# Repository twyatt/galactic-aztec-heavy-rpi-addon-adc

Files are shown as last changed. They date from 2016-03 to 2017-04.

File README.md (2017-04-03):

# About
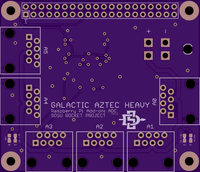
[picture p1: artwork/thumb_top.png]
OSHPark PCB Top Thumbnail

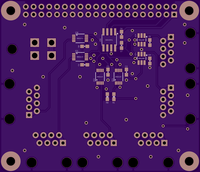
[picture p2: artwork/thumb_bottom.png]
OSHPark PCB Bottom Thumbnail


Custom Raspberry Pi Add-on ADC board (based on the [Galactic Aztec Raspberry Pi Add-on: Pressure Transducer Interface] board) used to read pressures on the [Galactic Aztec Heavy] rocket. The board has a molex connector for power input (Supply Voltage) and 6 ethernet ports for interfacing with custom [pressure transducer connector boards].

Custom EagleCAD parts on this board can be found in the [SDSU Rocket Eagle Libraries].

## Specifications
| Input | IC |
|:-----:|:---:|
| A0 | ADS1114 |
| A1 | ADS1114 |
| A2 | ADS1114 |
| A3 | ADS1114 |
| A4 | ADS1100 |
| A5 | ADS1100 |

### ADS1114
16-bit, 860 SPS ADC

| PGA | Resolution (V) | Maximum Input (V) |
|:---:|:---|:---:|
| 2/3 | 0.0001875 | 5.3 |
| 1 | 0.000125 | 4.096 |
| 2 | 0.0000625 | 2.048 |
| 4 | 0.00003125 | 1.024 |
| 8 | 0.000015625 | 0.512 |
| 16  | 0.0000078125 | 0.256 |

### ADS1100
| Bits | Resolution (V) | Sample Rate (SPS) |
|-----:|:---|:---:|
| 16 | 0.000152587891 | 8 |
| 15 | 0.000305175782 | 16 |
| 14 | 0.000610351563 | 32 |
| 12 | 0.00244140625  | 128 |

_Resolution values listed with PGA=1_

## Wiring
The ethernet ports adhere to the following [T-568B] wiring configuration:

| Pin | Color | Function |
|:---:|:---:|:---:|
| 1 | Orange/White | Signal |
| 2 | Orange | Signal |
| 3 | Green/White  | |
| 4 | Blue | Supply Voltage |
| 5 | Blue/White | Supply Voltage |
| 6 | Green | |
| 7 | Brown/White  | Ground |
| 8 | Brown | Ground |

# Bill of Materials
| Qty | Name  | Description | Notes | Part Number | Vendor |
|:---:|:-----:|---|---|---|---|
| 1 | H0 | Header Stacking 2x20 Tall 23mm | | [1979] | Adafruit |
| 1 | P0 | Molex Mini Fit Jr. 4-pos Right Angle | | [WM1352-ND] | DigiKey  |
| 6 | JP0-5 | Jack RJ45 CAT5/CAT5e | | [380-1046-ND] | DigiKey  |
| 1 | IC6 | ISO1541 Low-Power Bidirectional I²C Isolator | | [296-34872-1-ND] | DigiKey  |
| 4 | IC0-3 | ADS1114 16-Bit I²C Analog-to-Digital Converter | Addresses A0-A3 | [296-24932-1-ND] | DigiKey  |
| 1 | IC4 | ADS1100 16-Bit I²C Analog-to-Digital Converter | Address A4 (100) | [296-14301-1-ND] | DigiKey  |
| 1 | IC5 | ADS1100 16-Bit I²C Analog-to-Digital Converter | Address A5 (101) | [296-14302-1-ND] | DigiKey  |
| 2 | R0,1  | Resistor 1.8kΩ 1/10W ±1% 0603 | I²C Pull-up | [311-1.80KHRCT-ND] | DigiKey  |
| 8 | C0-7  | Capacitor Ceramic 0.1µF ±10% 25V 0603 | Bypass Capacitors | [490-1524-1-ND] | DigiKey  |
| 1 | D0 | LED Red Vf=1.8V If=2mA 0603 | 5V Power Indicator  | [475-1195-2-ND] | DigiKey  |
| 1 | R2 | Resistor 1.8kΩ 1/4W ±1% 0603 | | [P1.8KBYCT-ND] | DigiKey  |
| 1 | D1 | LED Yellow Vf=1.8V If=2mA 0603 | VIN Power Indicator | [475-1196-1-ND] | DigiKey  |
| 1 | R3 | Resistor 15kΩ 1/4W ±1% 0603 | | [RHM15.0KADCT-ND]  | DigiKey  |

[Galactic Aztec Raspberry Pi Add-on: Pressure Transducer Interface]: https://github.com/twyatt/galactic-aztec-rpi-addon-pressure
[Galactic Aztec Heavy]: http://rocket.sdsu.edu/rockets#galactic-aztec-heavy
[pressure transducer connector boards]: https://github.com/twyatt/galactic-aztec-pressure-transducer-connector
[SDSU Rocket Eagle Libraries]: https://github.com/twyatt/SDSURocket-Eagle-Libraries
[T-568B]: https://en.wikipedia.org/wiki/TIA/EIA-568#Wiring
[1979]: https://www.adafruit.com/product/1979
[WM1352-ND]: http://www.digikey.com/product-detail/en/0039301040/WM1352-ND/561079
[380-1046-ND]: http://www.digikey.com/product-detail/en/SS-7188-NF/380-1046-ND/388308
[296-34872-1-ND]: http://www.digikey.com/product-detail/en/texas-instruments/ISO1541DR/296-34872-1-ND/3587215
[296-24932-1-ND]: http://www.digikey.com/product-detail/en/texas-instruments/ADS1114IDGST/296-24932-1-ND/2123296
[296-14301-1-ND]: http://www.digikey.com/product-detail/en/texas-instruments/ADS1100A4IDBVT/296-14301-1-ND/528555
[296-14302-1-ND]: http://www.digikey.com/product-detail/en/texas-instruments/ADS1100A5IDBVT/296-14302-1-ND/528553
[311-1.80KHRCT-ND]: http://www.digikey.com/product-detail/en/yageo/RC0603FR-071K8L/311-1.80KHRCT-ND/729821
[490-1524-1-ND]: http://www.digikey.com/product-detail/en/murata-electronics-north-america/GRM188R71E104KA01D/490-1524-1-ND/587865
[475-1195-2-ND]: http://www.digikey.com/product-detail/en/LS%20L29K-H1J2-1-Z/475-1195-1-ND/810356
[P1.8KBYCT-ND]: http://www.digikey.com/product-detail/en/ERJ-PA3F1801V/P1.8KBYCT-ND/5036145
[475-1196-1-ND]: http://www.digikey.com/product-detail/en/LY%20L29K-H1K2-26-Z/475-1196-1-ND/810357
[RHM15.0KADCT-ND]: http://www.digikey.com/product-detail/en/rohm-semiconductor/ESR03EZPF1502/RHM15.0KADCT-ND/1983758

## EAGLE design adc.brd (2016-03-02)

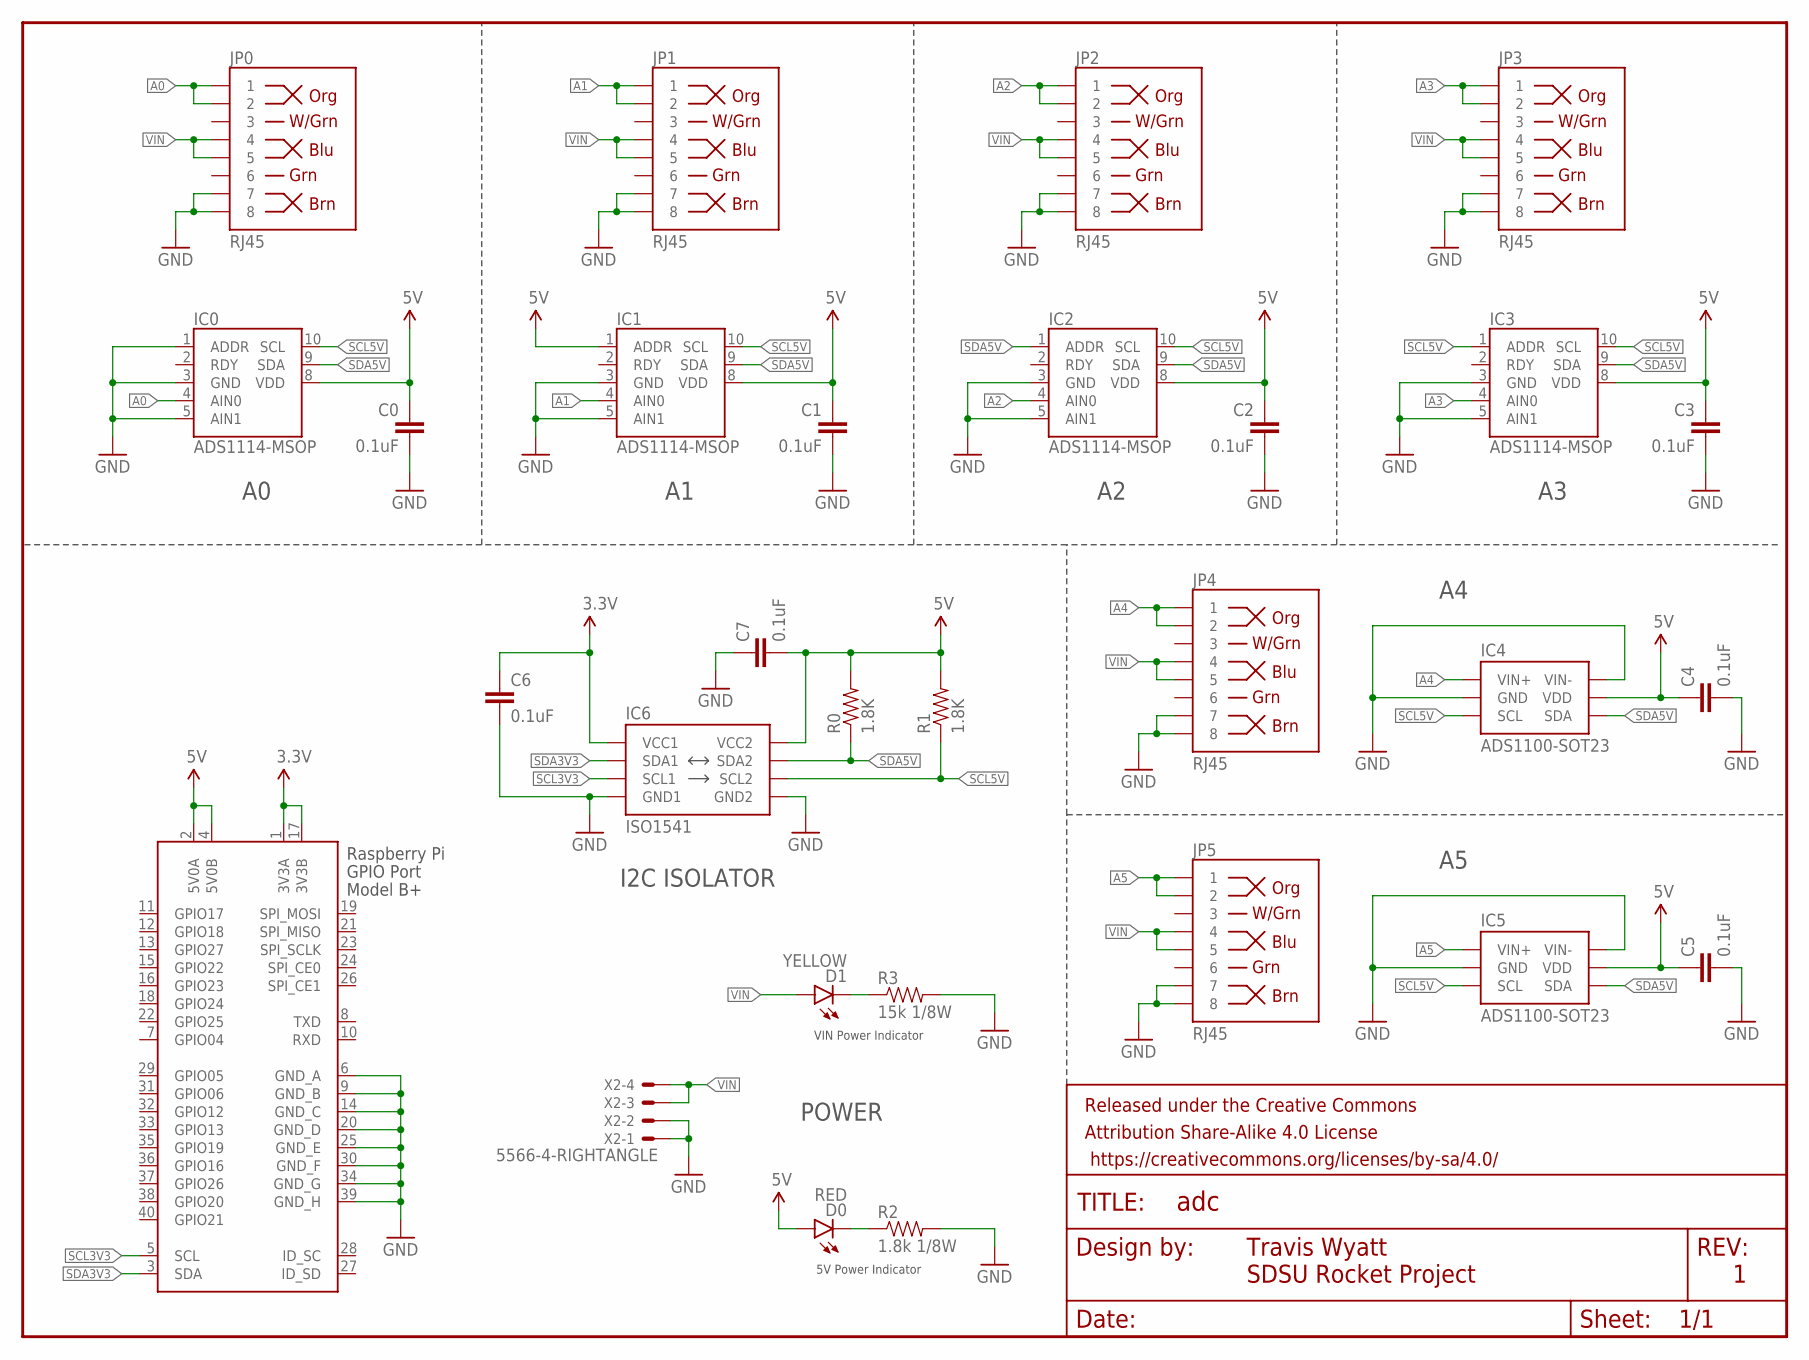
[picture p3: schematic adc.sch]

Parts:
C0, C1, C2, C3, C4, C5, C6, C7: 0.1uF; 0603-CAP
D0: RED; LED-0603
D1: YELLOW; LED-0603
FRAME1: FRAME-LETTER; CREATIVE_COMMONS
IC0, IC1, IC2, IC3: ADS1114-MSOP; MSOP10
IC4, IC5: ADS1100-SOT23; SOT23-6
IC6: ISO1541; SOIC8
JP0, JP1, JP2, JP3, JP4, JP5: RJ45; RJ45-8
R0, R1: 1.8K; 0603-RES
R2: 1.8k 1/8W; 0603-RES
R3: 15k 1/8W; 0603-RES
X1: RASPI_BOARD_B+#_H; RASPI_BOARD_B+HAT
X2: 5566-4-RIGHTANGLE; 5566-4

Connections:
3.3V: C6.1, IC6.1 (VCC1), X1.1 (3V3A), X1.17 (3V3B)
5V: C0.1, C1.1, C2.1, C3.1, C4.1, C5.1, C7.2, D0.A, IC0.8 (VDD), IC1.1 (ADDR), IC1.8 (VDD), IC2.8 (VDD), IC3.8 (VDD), IC4.5 (VDD), IC5.5 (VDD), IC6.8 (VCC2), R0.2, R1.2, X1.2 (5V0A), X1.4 (5V0B)
A0: IC0.4 (AIN0), JP0.1, JP0.2
A1: IC1.4 (AIN0), JP1.1, JP1.2
A2: IC2.4 (AIN0), JP2.1, JP2.2
A3: IC3.4 (AIN0), JP3.1, JP3.2
A4: IC4.1 (VIN+), JP4.1, JP4.2
A5: IC5.1 (VIN+), JP5.1, JP5.2
GND: C0.2, C1.2, C2.2, C3.2, C4.2, C5.2, C6.2, C7.1, IC0.1 (ADDR), IC0.3 (GND), IC0.5 (AIN1), IC1.3 (GND), IC1.5 (AIN1), IC2.3 (GND), IC2.5 (AIN1), IC3.3 (GND), IC3.5 (AIN1), IC4.2 (GND), IC4.6 (VIN-), IC5.2 (GND), IC5.6 (VIN-), IC6.4 (GND1), IC6.5 (GND2), JP0.7, JP0.8, JP1.7, JP1.8, JP2.7, JP2.8, JP3.7, JP3.8, JP4.7, JP4.8, JP5.7, JP5.8, R2.2, R3.2, X1.6 (GND_A), X1.9 (GND_B), X1.14 (GND_C), X1.20 (GND_D), X1.25 (GND_E), X1.30 (GND_F), X1.34 (GND_G), X1.39 (GND_H), X2.1, X2.2
unnamed: D1.C, R3.1
unnamed: D0.C, R2.1
SCL3V3: IC6.3 (SCL1), X1.5 (SCL)
SCL5V: IC0.10 (SCL), IC1.10 (SCL), IC2.10 (SCL), IC3.1 (ADDR), IC3.10 (SCL), IC4.3 (SCL), IC5.3 (SCL), IC6.6 (SCL2), R1.1
SDA3V3: IC6.2 (SDA1), X1.3 (SDA)
SDA5V: IC0.9 (SDA), IC1.9 (SDA), IC2.1 (ADDR), IC2.9 (SDA), IC3.9 (SDA), IC4.4 (SDA), IC5.4 (SDA), IC6.7 (SDA2), R0.1
VIN: D1.A, JP0.4, JP0.5, JP1.4, JP1.5, JP2.4, JP2.5, JP3.4, JP3.5, JP4.4, JP4.5, JP5.4, JP5.5, X2.3, X2.4

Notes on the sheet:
Travis Wyatt
SDSU Rocket Project
POWER
5V Power Indicator
VIN Power Indicator
I2C ISOLATOR

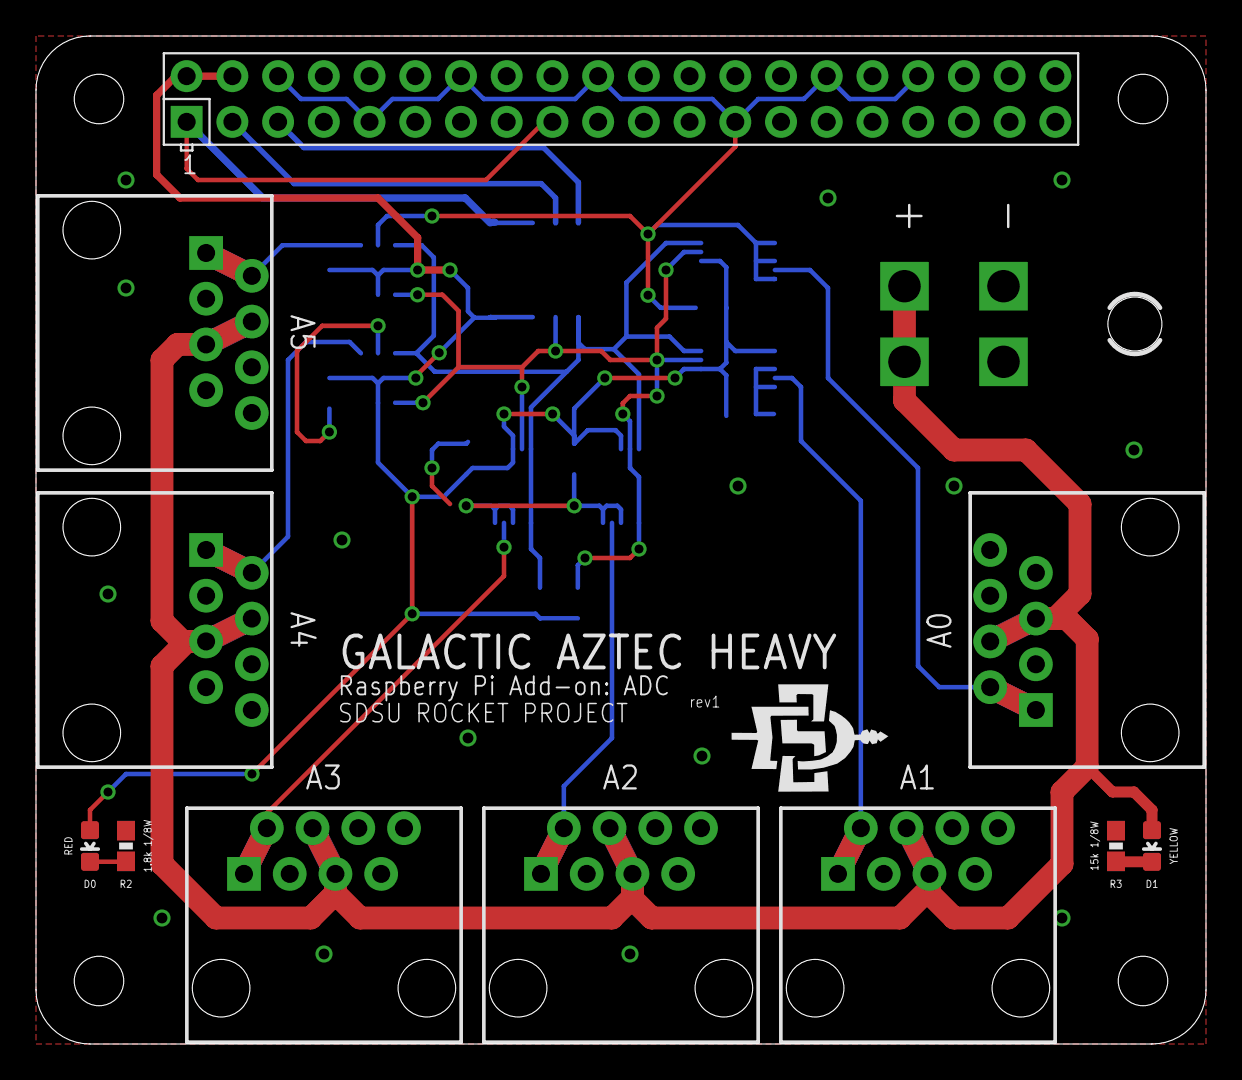
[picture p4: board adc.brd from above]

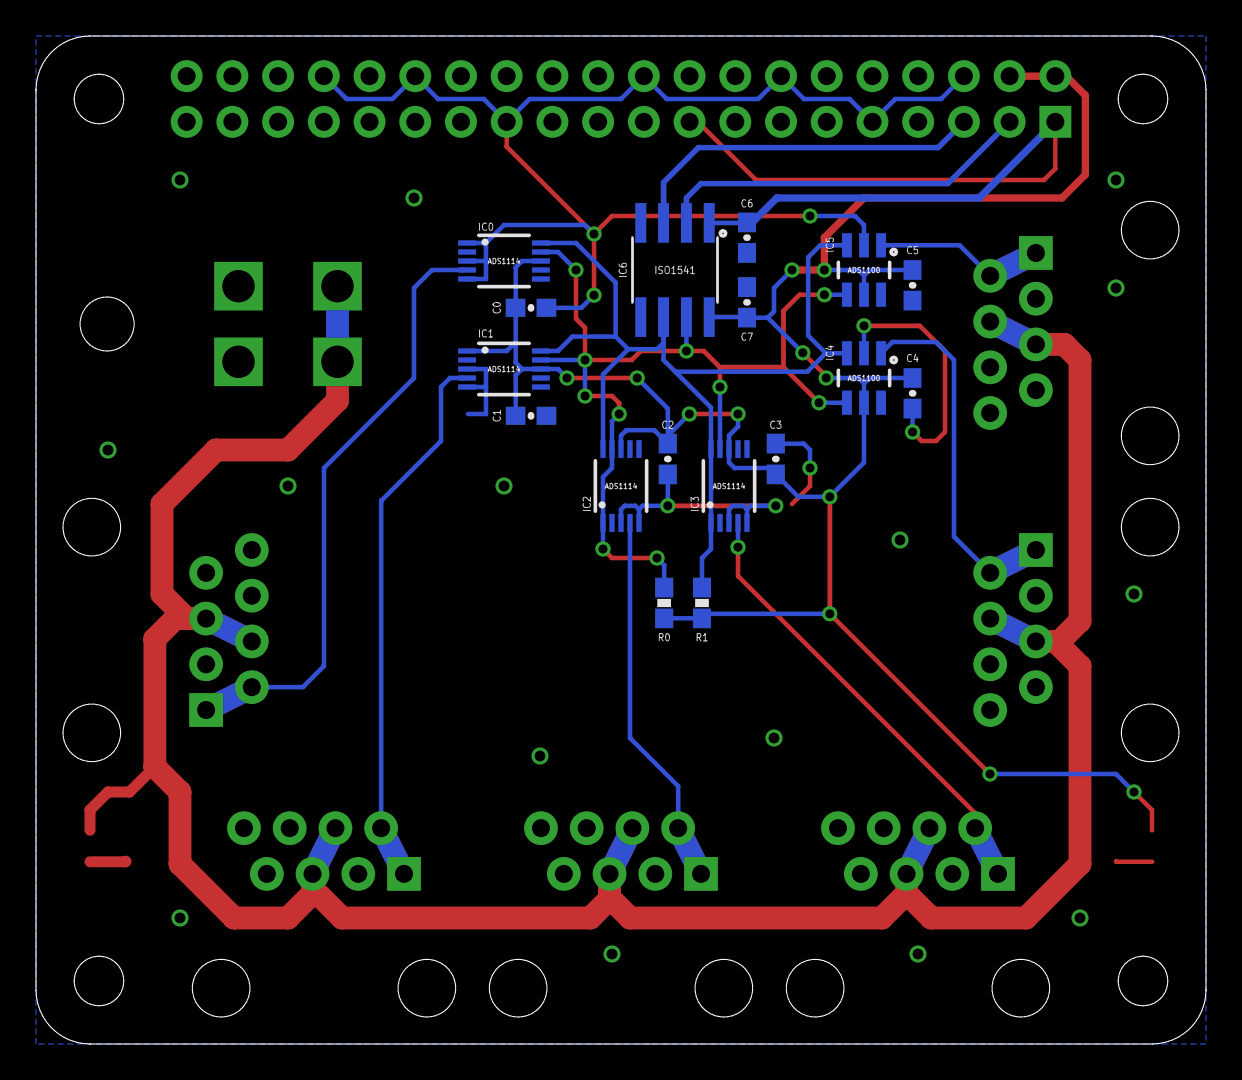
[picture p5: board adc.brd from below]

Board: 2 copper layers, 65.0 x 56.0 mm, 30 parts (17 on the bottom side), 16 nets.

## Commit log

2016-03-02 Initial commit
    Created schematic and 2-layer board for Raspberry Pi Add-on: ADC.
    [adc.brd, adc.sch]
2016-03-02 Fix pressure transducer interface link
2016-03-20 Add ADC specifications to readme

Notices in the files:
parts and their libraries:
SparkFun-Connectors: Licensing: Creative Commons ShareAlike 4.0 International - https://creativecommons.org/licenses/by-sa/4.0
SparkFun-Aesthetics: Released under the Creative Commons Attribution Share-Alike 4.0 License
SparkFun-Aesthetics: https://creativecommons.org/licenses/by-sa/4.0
